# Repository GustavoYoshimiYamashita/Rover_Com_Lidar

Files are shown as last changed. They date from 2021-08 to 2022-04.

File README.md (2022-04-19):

# Rover_Com_Lidar
Um robô do tipo Rover com estrutura Rocker-bogie acoplado com um sensor Lidar
Avanço do Rover durante o ano de 2021

Etapas de desenvolvimento
1.	Estudo dos componentes eletrônicos necessários
2.	Modelagem 3D
3.	Desenvolvimento da montagem das peças
4.	Primeiros testes com o Lidar
5.	Primeiros testes com a estrutura Rocker-Bogie
6.	Modelagem de um sistema de encoders para as rodas
7.	Novo estudo sobre os microcontroladores e formas de comunicação
8.	Atualização e refinação da estrutura Rocker-Bogie
9.	Testes com a estrutura enfrentando desafios
10.	Correção de problemas com as rodas
11.	Correção do Motor de passo
12.	Estudo da geração de mapas para a visualização da nuvem de pontos do Lidar
13.	Novos testes com o Lidar funcionando
14.	Etapas completas, necessário o desenvolvimento de soluções para possíveis erros
15.	Problema “ainda” sem solução no giro da estrutura Rocker-Bogie
Componentes eletrônicos utilizados

## Modelagem 3D
Antes da aquisição dos materiais necessários para a montagem do Rover foi desenvolvido em um programa de modelagem 3D AutoCAD (SolidWorks) uma simulação da estrutura Rocker-Bogie, essa simulação permitiu uma visualização mais detalhada da aparência e dimensões finais do projeto antes mesmo da montagem. 

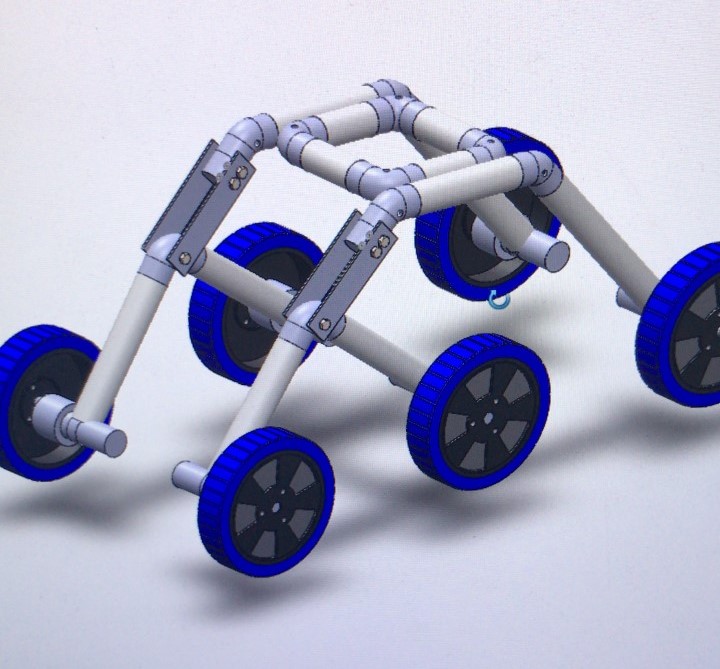
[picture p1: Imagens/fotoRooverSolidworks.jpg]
 
 
Dessa forma todo o processo pode ser visualizado de maneira que seja possível evitar erros na quantidade, formato ou tamanho dos materiais que serão utilizados, a importância dessa etapa está em precisar os custos do projeto e diminuir as chances de desperdício de tempo na correção de possíveis erros futuros decorrentes de uma visualização não apurada da montagem.

## Montagem e problemas iniciais 
Com base na modelagem 3D é possível iniciar a montagem seguindo o desenho como referência. Na primeira etapa então foi feito os cortes nos canos para o tamanho adequado, é importante destacar que se viu necessário manter uma das pontas reta com o mínimo de deformação, tendo em vista que essa parte se conectaria com o motor e qualquer desvio na estrutura deixaria o motor desalinhado e com o seu giro prejudicado quando comparado com os outros motores.
Sem um kit profissional de corte e lixamento o processo se torna demorado e cansativo, porém é possível ser realizado utilizando-se de ferramentas como serras e lixas de papel.

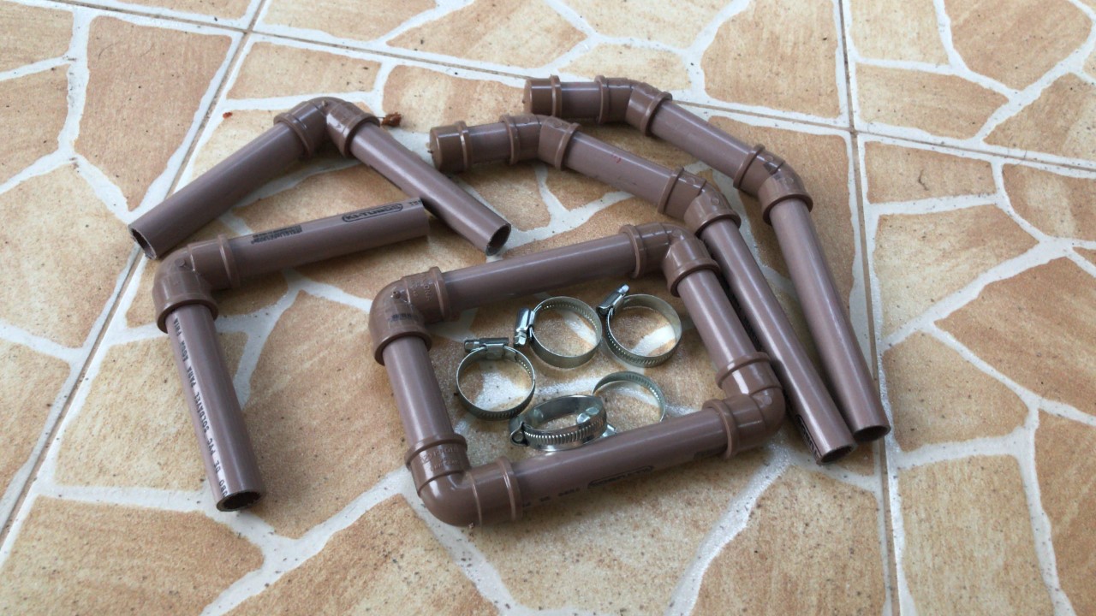
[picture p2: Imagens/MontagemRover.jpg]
Foto da montagem


Com os cortes feitos, bastava apenas a montagem.

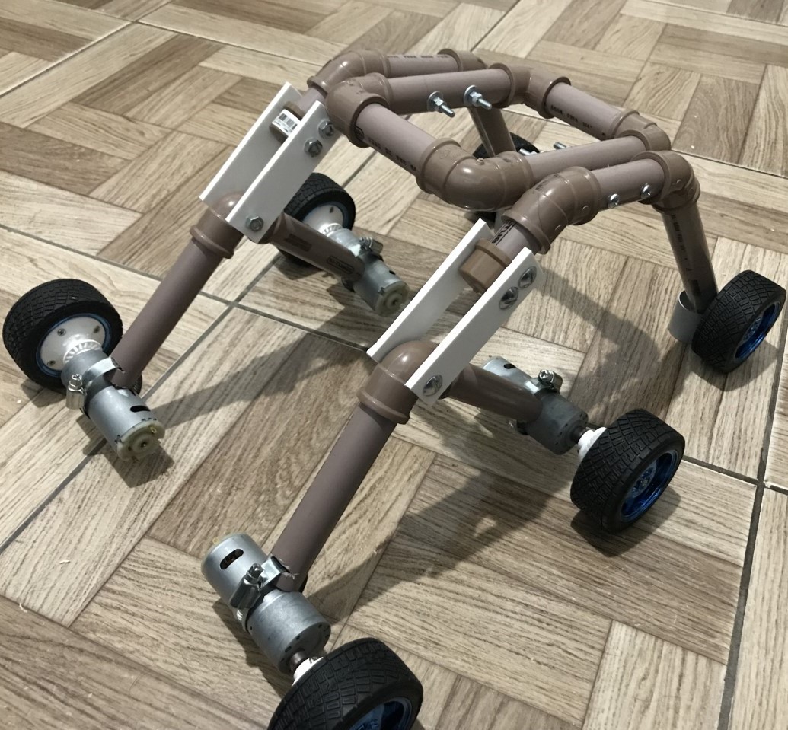
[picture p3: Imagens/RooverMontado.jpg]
Foto do rover montado

 
A montagem ficou idêntica a simulação feita no SolidWorks, porém, nos primeiros testes realizados ficou evidente alguns problemas da estrutura. Os furos no qual passavam os parafusos que conectavam as partes de cima estavam desalinhados e por isso ocasionaram um erro que impedia a realização de movimentos mais complexos como por exemplo subir uma escada. 
As rodas evidenciaram outro problema ocasionado pelo método escolhido para prender a roda com o motor, o eixo do motor estava deslizando sem prender na roda, dessa forma, quando o motor se encontrava em uma região de alto atrito ou que necessitava de um alto torque as rodas giravam e falso.
No lidar a estrutura se comportou de maneira no qual havia sido prevista, não demonstrando então problemas ou erros aparentes.

Foto do Lidar montado
 
Um desafio enfrentado no projeto foi nos testes realizados no motor de passo Nema 17, que ao comprar pela internet possuía em suas características um certo nível de torque mais que necessário para a estrutura em si, porém, quando o pacote chegou o motor se demonstrou diferente das características anunciadas. Devido a esse motivo a etapa de desenvolvimento do Lidar foi prejudica, já que foram testados diversos códigos diferentes com o pensamento de que o problema não era no hardware (por causa da falsa informação do anúncio), por fim foi decidido a compra de um novo motor de passo do tipo Nema 17 que não apresentou problema nenhum e funcionou perfeitamente.
Desenvolvimento da estrutura Rocker-Bogie

O falso giro das rodas impedia que o robô conseguisse executar tarefas mais difíceis como subir escadas, superar obstáculos e se movimentar em terrenos irregulares. A solução encontrada para este problema foi modelar um encaixe que se prendesse ao eixo do motor sem a necessidade de um parafuso ou material adesivo, para isso foi desenhado a entrada do suporte com o mesmo formato e dimensão do eixo do motor.
Para corrigir o desalinhamento da estrutura Rocker-Bogie foi necessário reconstruir todo o robô com novos materiais, além disso foi utilizado um cano mais grosso já que no primeiro caso a ruptura de alguns pontos eram comuns devido a espessura dos canos antes utilizados, dessa forma, a substituição dos materiais serviu não apenas para corrigir o alinhamento, mas também para garantir maior resistência do robô.

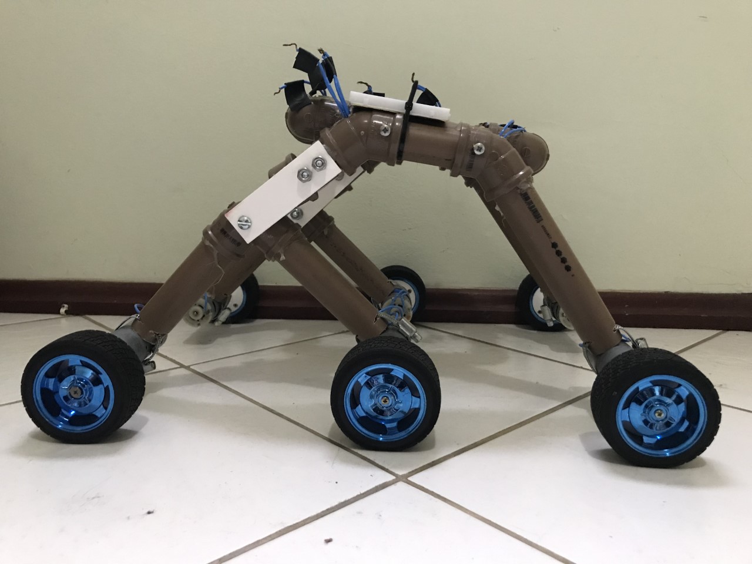
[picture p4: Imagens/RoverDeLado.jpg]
Foto da versão 2 do Rover

 
Nesse novo modelo a estrutura se apresentou eficiente no desenvolvimento de obstáculos e caminhos mais complexos, com os 6 motores somando um total de 60kg de torque, não houve nenhum problema de movimentação decorrente do peso total do robô. 

## Desenvolvimento do Lidar

O objetivo do Lidar era criar uma nuvem de pontos provenientes das leituras do sensor Infravermelho utilizado, o TF-Luna. Esse sensor possui um alcance significativamente alto quando comparado com outros modelos encontrados para comprar, com uma leitura de 8 metros esse sensor é capaz de mapear ambientes grandes sem a necessidade de se deslocar.
No começo do projeto foi pensado em utilizar algum sistema para enviar as leituras do sensor via bluetooth ou Wifi, com o objetivo de proporcionar maior articulação sem a necessidade do uso de algum fio de conexão, no entanto, foi optado o uso de uma conexão USB com o computador pois alguns problemas de envio de dados estavam sendo enfrentados na opção de Wifi ou Bluetooth. Dessa forma, o Lidar está funcionando conectado por um cabo USB ao computador, porém, isso foi previsto e pensado como uma situação coerente com o desenvolvimento do projeto esse ano, com o objetivo de nos próximos passos modificar a estrutura lógica para então utilizar um sistema sem fio. Pela imagem abaixo podemos ver o Lidar conectado ao computador.

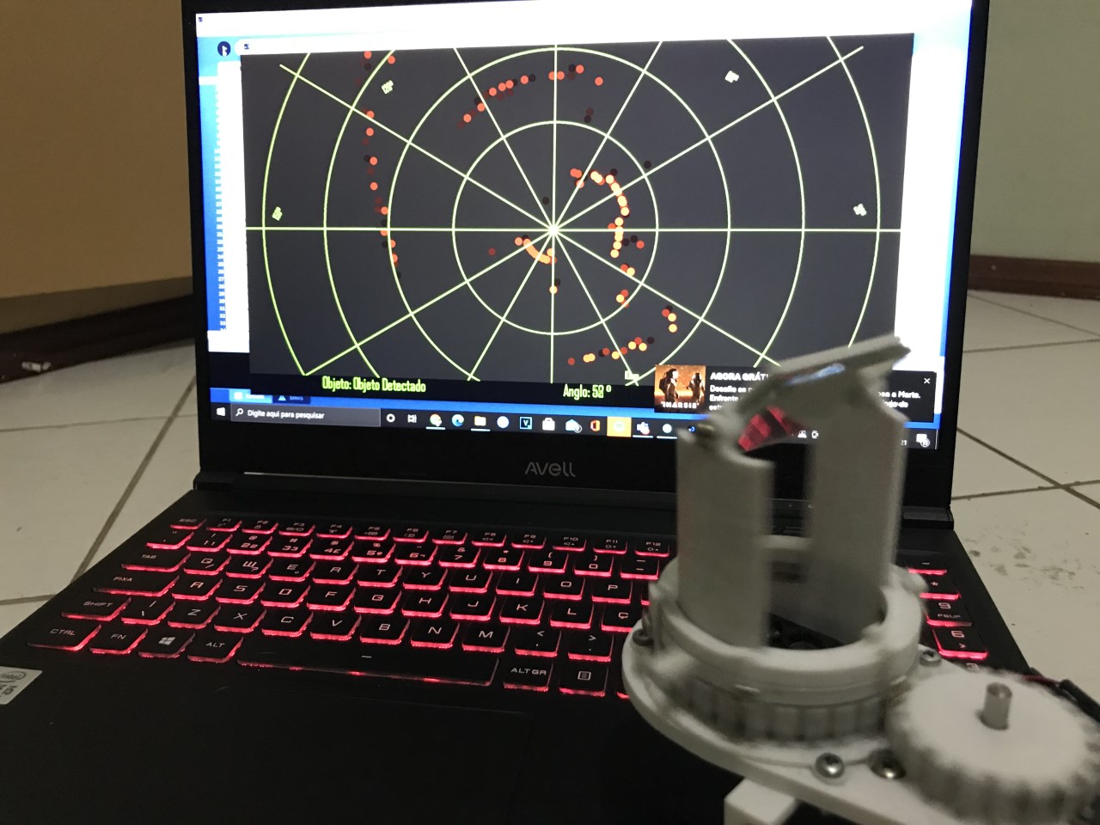
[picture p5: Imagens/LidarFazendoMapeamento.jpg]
Picture of the 3D lidar


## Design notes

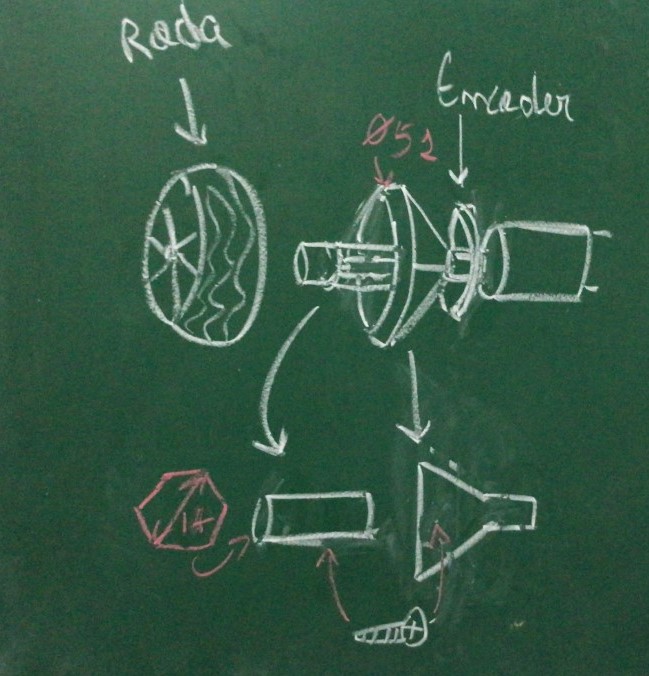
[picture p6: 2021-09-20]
Imagens/LousaDesenhos.jpg

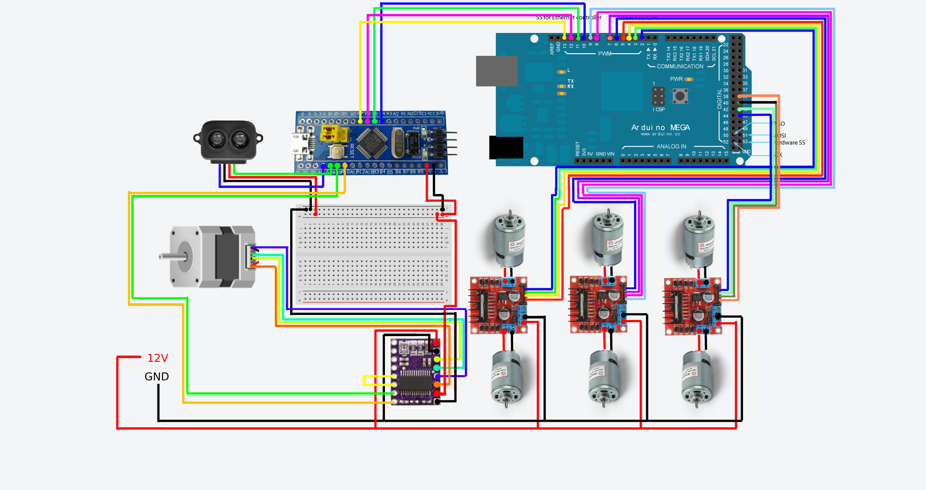
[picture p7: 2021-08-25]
Circuito/Circuito Principal/conexõesRover.png

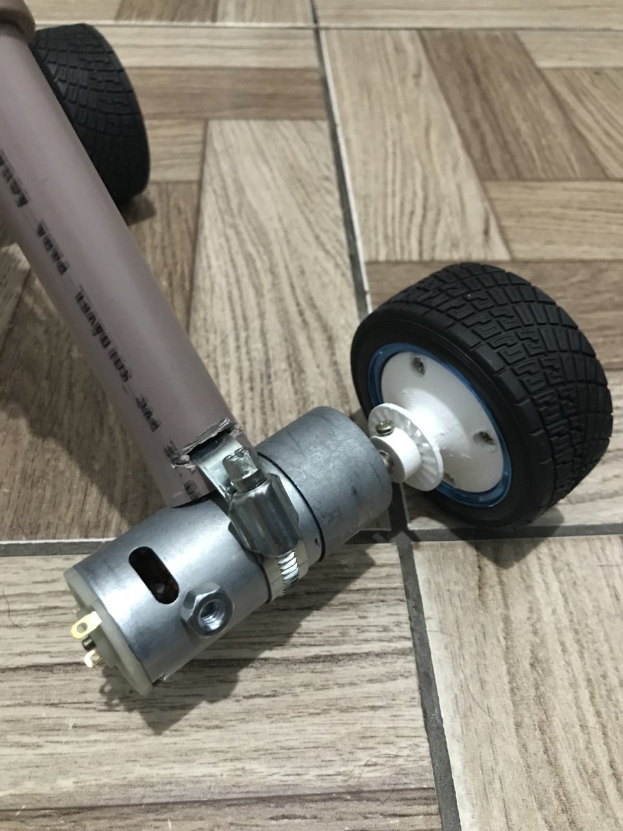
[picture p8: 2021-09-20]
Imagens/encaixeCompletoRodas.jpg

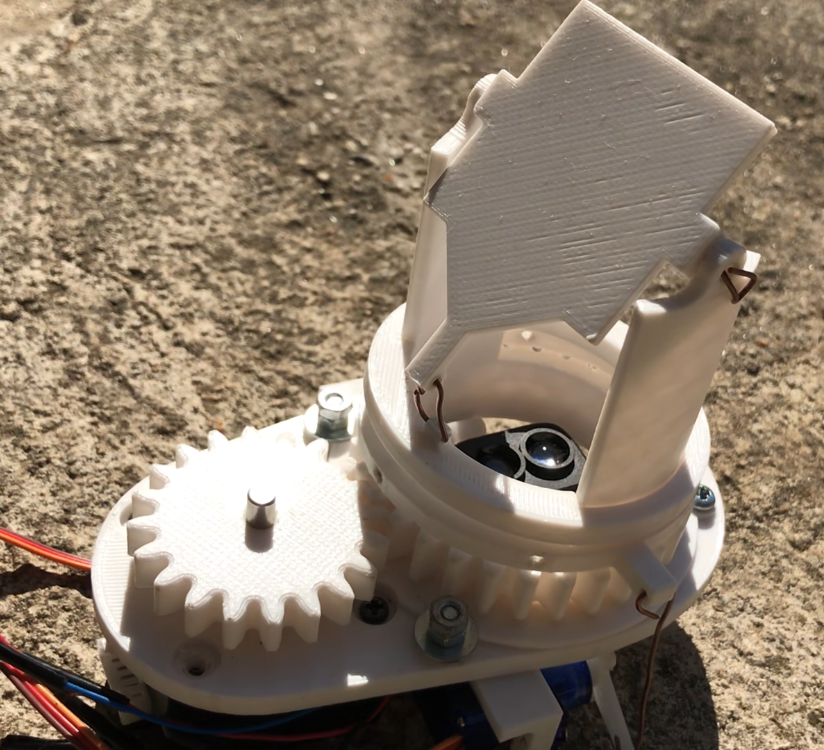
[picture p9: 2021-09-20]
Imagens/Foto1Lidar.png

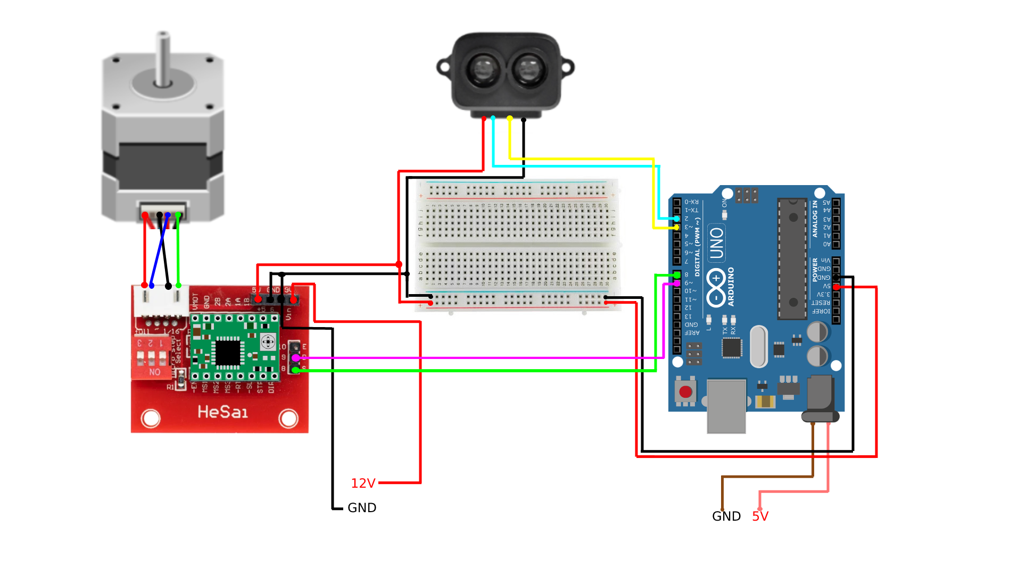
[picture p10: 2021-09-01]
Circuito/Circuito Lidar-Motor De Passo-Arduino/Novo Projeto.png

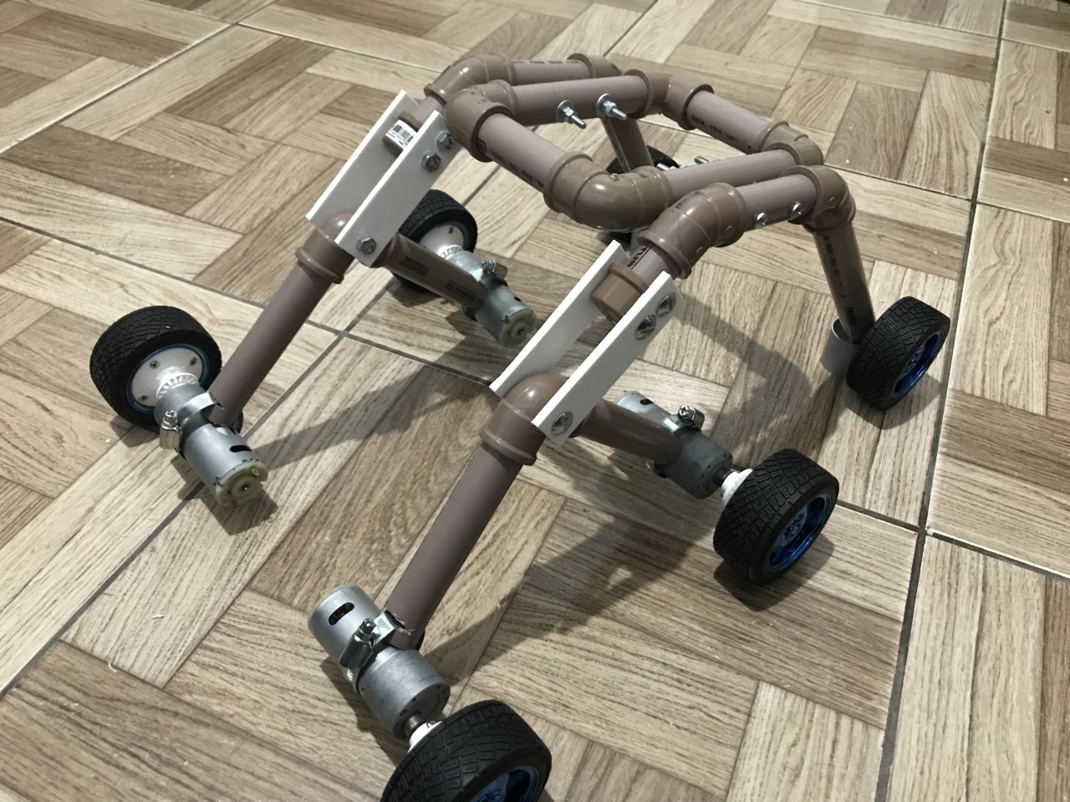
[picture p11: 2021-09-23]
Imagens/roverComProblema.jpg

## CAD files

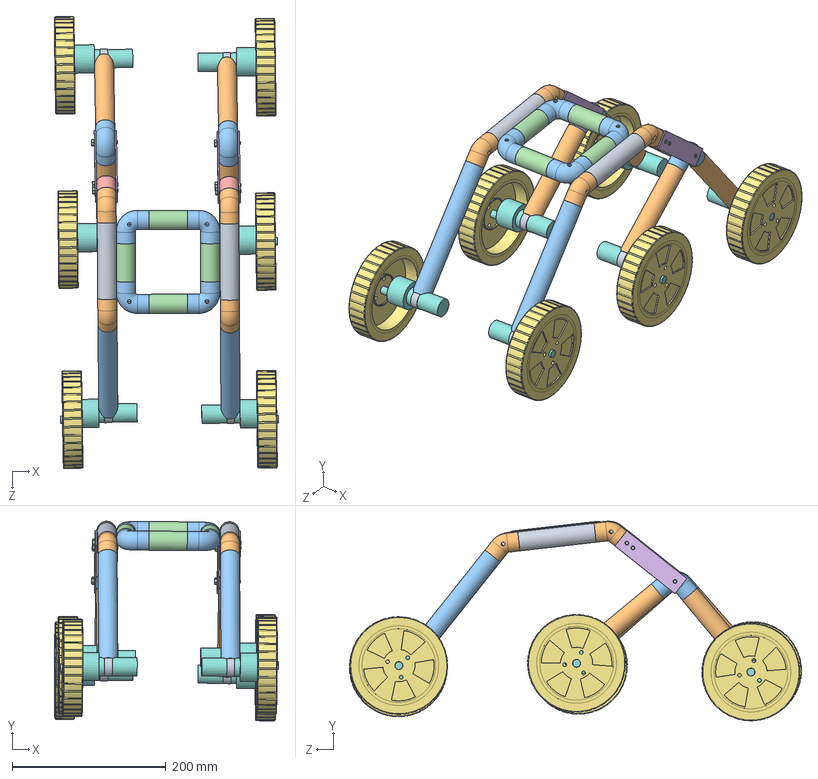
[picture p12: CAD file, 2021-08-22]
Partes 3D/Rover/Montagem1.SLDASM
292.2 x 260.0 x 588.8 mm
Cano10cm x 2
Cotovelo45graus x 4
Cotovelo90graus x 6
hex cap screw_am x 6
CapaPVC x 2
placaDeApoio x 4
Cytron 5 Inches Robot Wheel x 6
Motor12VDC x 6
EnforcaGato x 6
Cano13cm x 4
Cano18cm x 2
Cano5cm x 4

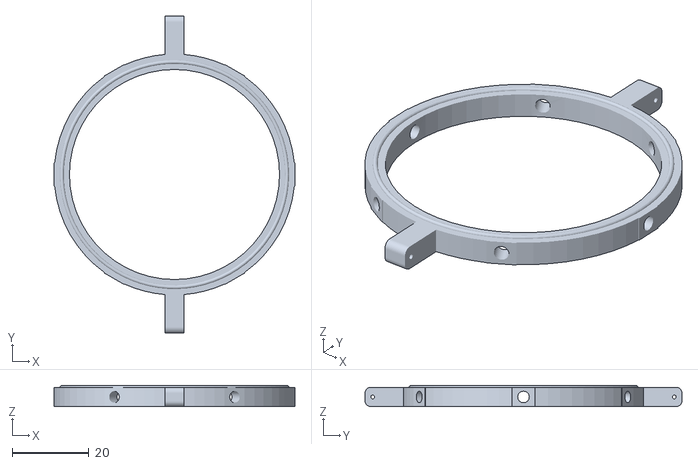
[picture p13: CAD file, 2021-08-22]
Partes 3D/Lidar/LidarMK2-Ring_bot.STL
62.6 x 82.4 x 5.50

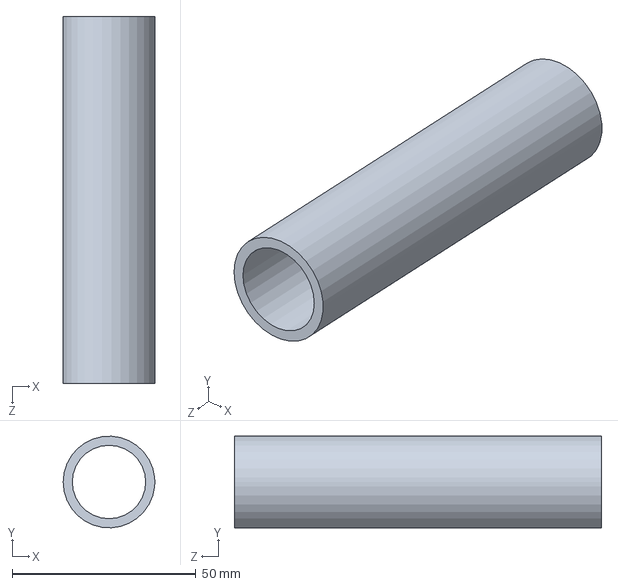
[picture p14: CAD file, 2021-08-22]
Partes 3D/Rover/Cano10cm.SLDPRT
25.0 x 25.0 x 100.0 mm

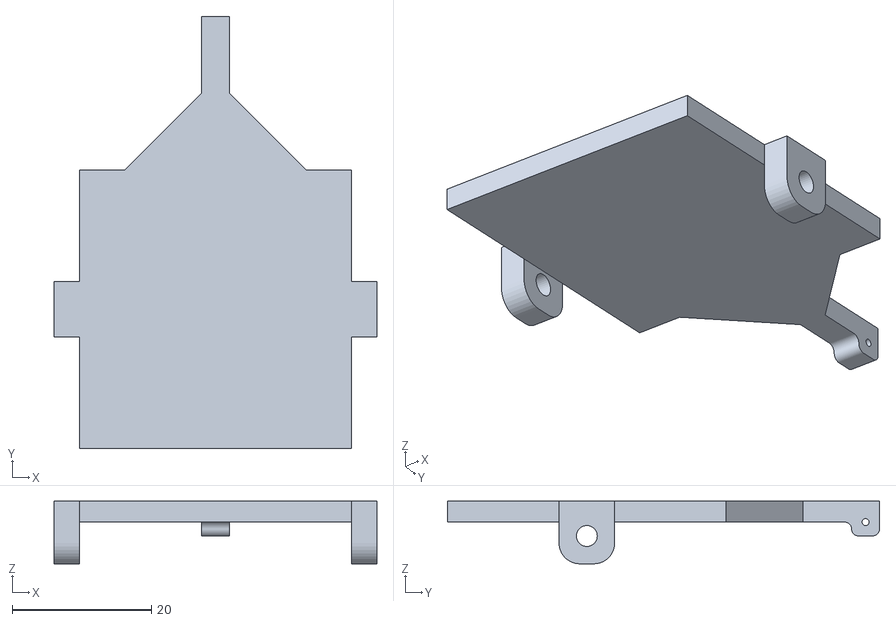
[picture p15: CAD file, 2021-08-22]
Partes 3D/Lidar/LidarMK2-Mirror.STL
46.3 x 62.0 x 9.00

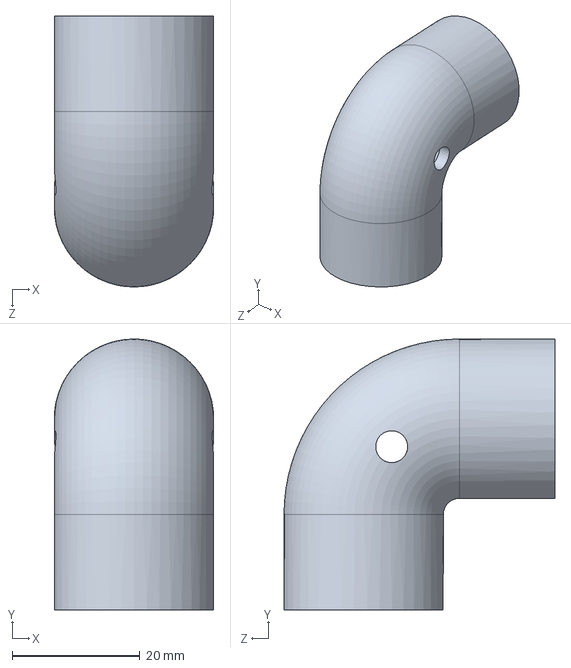
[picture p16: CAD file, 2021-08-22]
Partes 3D/Rover/Cotovelo90graus.SLDPRT
25.0 x 42.5 x 42.5 mm

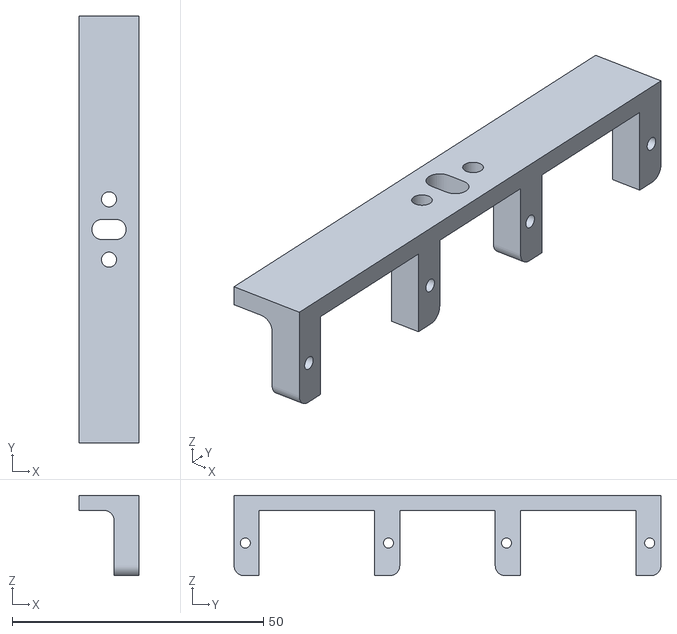
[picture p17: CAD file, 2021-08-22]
Partes 3D/Lidar/LidarMK2-Servos.STL
12.0 x 85.0 x 16.0

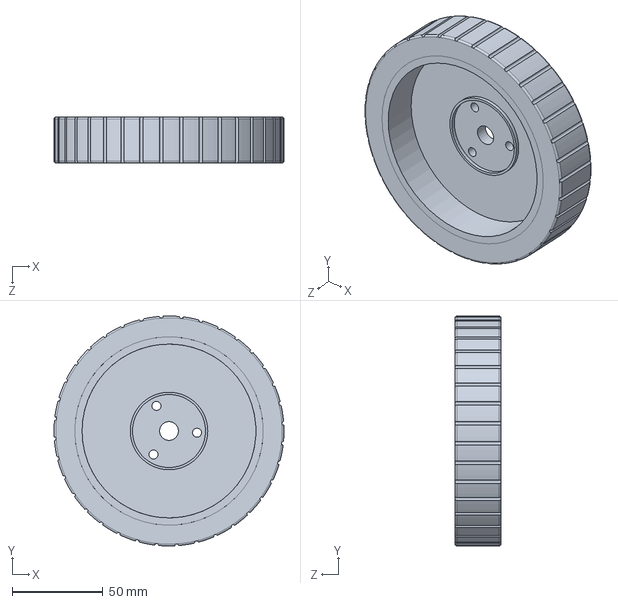
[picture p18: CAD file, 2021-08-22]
Partes 3D/Rover/Cytron 5 Inches Robot Wheel.SLDPRT
127.0 x 127.0 x 25.4 mm

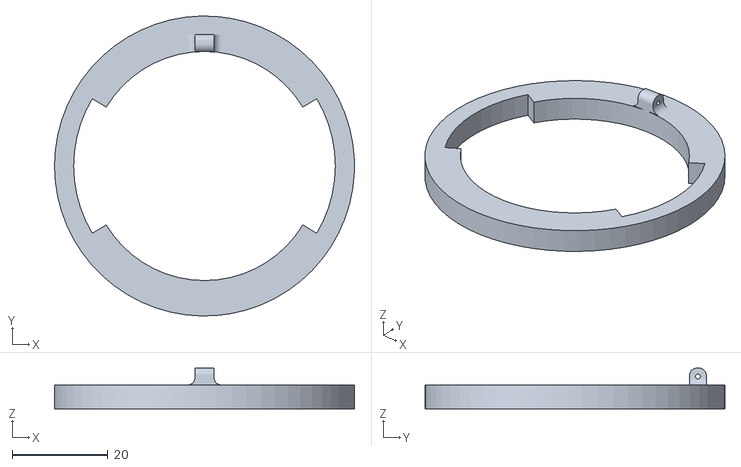
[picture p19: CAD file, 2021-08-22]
Partes 3D/Lidar/LidarMK2-Ring_top.STL
62.6 x 62.6 x 8.50

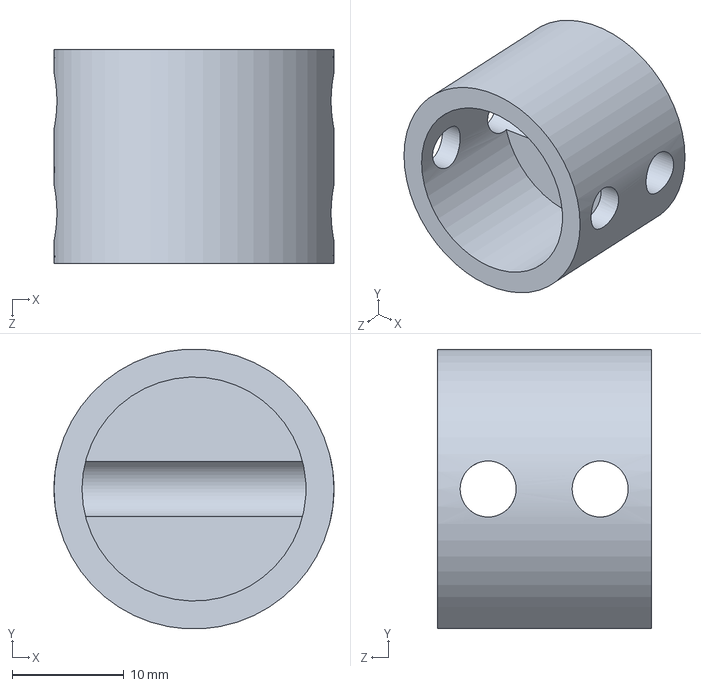
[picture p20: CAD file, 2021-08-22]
Partes 3D/Rover/CapaPVC.SLDPRT
25.0 x 25.0 x 19.1 mm

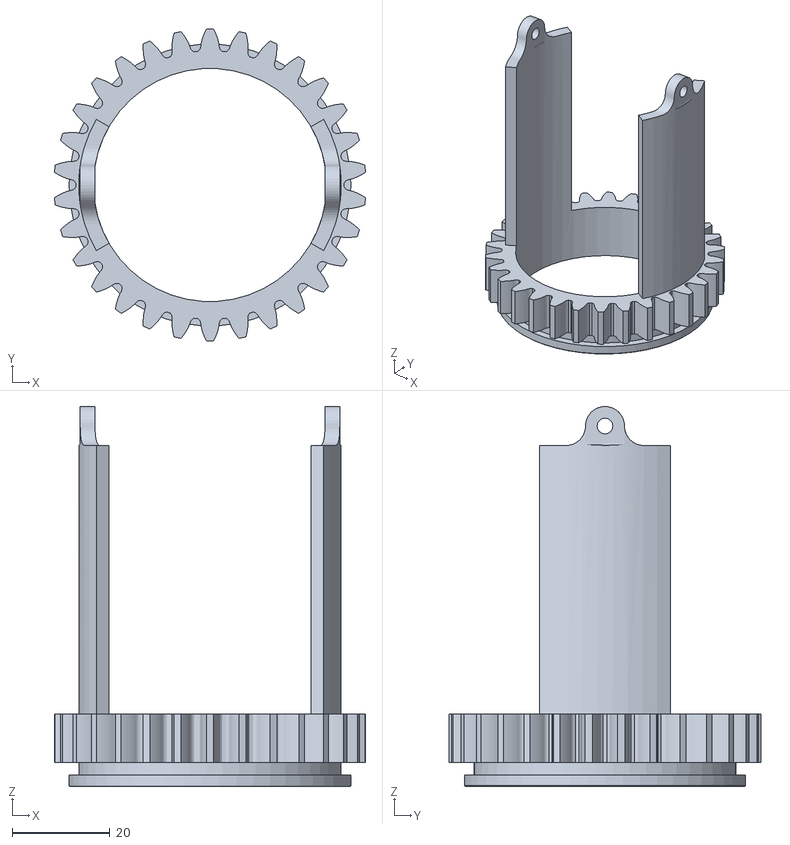
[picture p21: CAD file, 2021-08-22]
Partes 3D/Lidar/LidarMK2-Rotor.STL
63.8 x 64.0 x 77.9

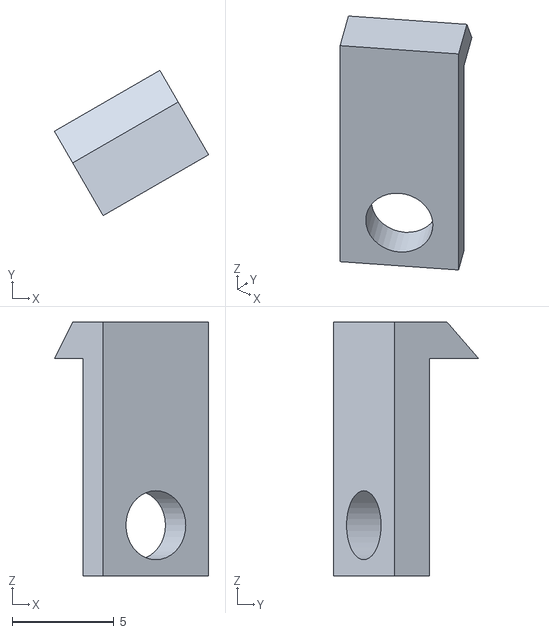
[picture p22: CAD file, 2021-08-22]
Partes 3D/Lidar/LidarMK2-Ring_link.STL
7.60 x 7.16 x 12.5

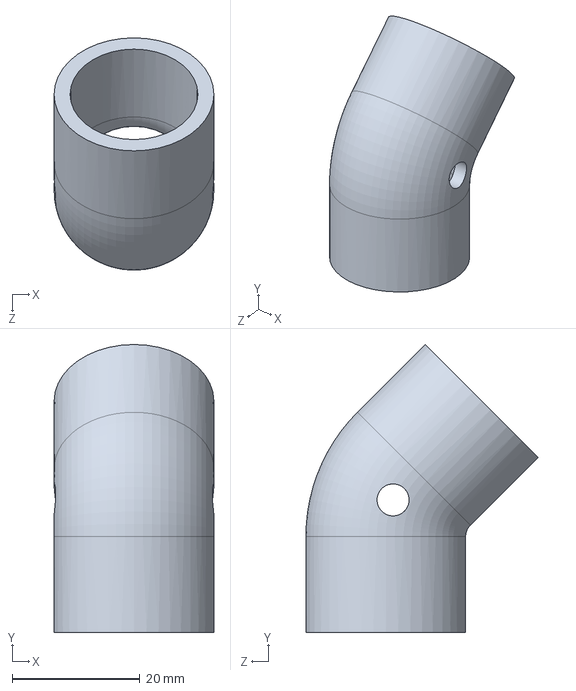
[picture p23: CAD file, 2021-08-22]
Partes 3D/Rover/Cotovelo45graus.SLDPRT
25.0 x 45.1 x 36.3 mm

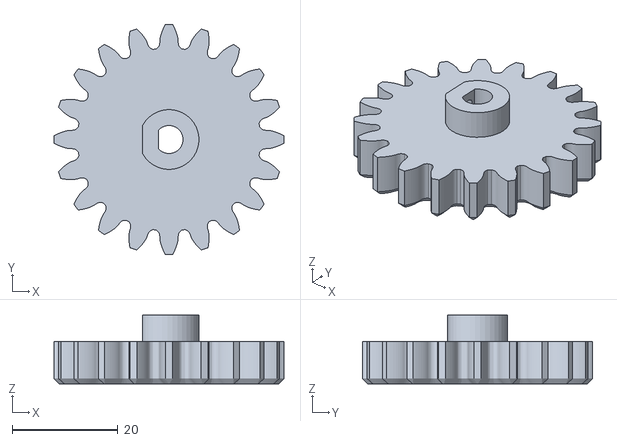
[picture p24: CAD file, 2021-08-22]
Partes 3D/Lidar/LidarMK2-GearMotor.STL
43.4 x 43.4 x 13.0

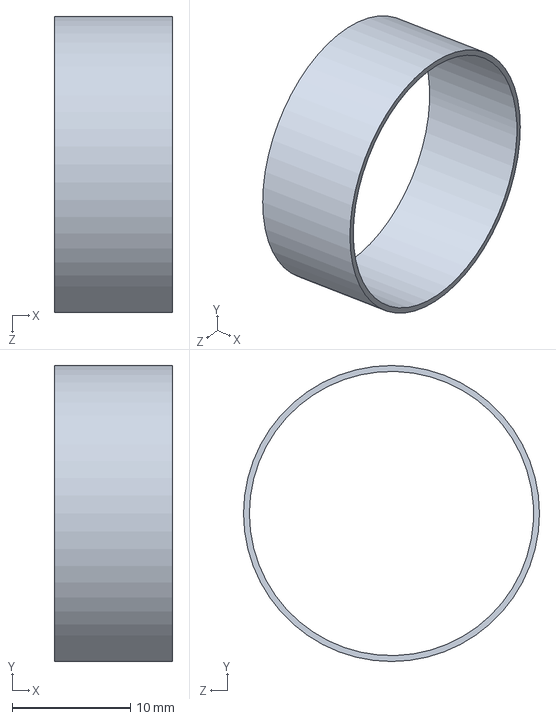
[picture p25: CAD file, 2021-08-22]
Partes 3D/Rover/EnforcaGato.SLDPRT
10.0 x 25.0 x 25.0 mm

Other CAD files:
Partes 3D/Lidar/LidarMK2-Base.STL
Partes 3D/Rover/Cano5cm.SLDPRT
Partes 3D/Lidar/LidarMK2.SLDPRT
Partes 3D/Rover/Cano9cm.SLDPRT
Partes 3D/Lidar/LidarMK2-Rotor _holder.STL
Partes 3D/Rover/Cano13cm.SLDPRT
Partes 3D/Rover/Cano15cm.SLDPRT
Partes 3D/Rover/Cano18cm.SLDPRT
Partes 3D/Rover/Motor12VDC.SLDPRT
Partes 3D/Rover/placaDeApoio.SLDPRT

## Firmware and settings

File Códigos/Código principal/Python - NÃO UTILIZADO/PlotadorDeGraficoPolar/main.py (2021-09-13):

# Python + Arduino-based Radar Plotter
#
# ** Works with any motor that outputs angular rotation
# ** and with any distance sensor (HC-SR04, VL53L0x,LIDAR)
#
import numpy as np
import matplotlib

matplotlib.use('TkAgg')
import matplotlib.pyplot as plt
from matplotlib.widgets import Button
import serial, sys, glob
import serial.tools.list_ports as COMs


#
#
############################################
# Find Arudino ports, select one, then start communication with it
############################################
#
def port_search():
    if sys.platform.startswith('win'):  # Windows
        ports = ['COM{0:1.0f}'.format(ii) for ii in range(1, 256)]
    elif sys.platform.startswith('linux') or sys.platform.startswith('cygwin'):
        ports = glob.glob('/dev/tty[A-Za-z]*')
    elif sys.platform.startswith('darwin'):  # MAC
        ports = glob.glob('/dev/tty.*')
    else:
        raise EnvironmentError('Machine Not pyserial Compatible')

    arduinos = []
    for port in ports:  # loop through to determine if accessible
        if len(port.split('Bluetooth')) > 1:
            continue
        try:
            ser = serial.Serial(port)
            ser.close()
            arduinos.append(port)  # if we can open it, consider it an arduino
        except (OSError, serial.SerialException):
            pass
    return arduinos


arduino_ports = port_search()
ser = serial.Serial(arduino_ports[1], baudrate=115200)  # match baud on Arduino
ser.flush()  # clear the port
#
############################################
# Start the interactive plotting tool and
# plot 180 degrees with dummy data to start
############################################
#
fig = plt.figure(facecolor='k')
win = fig.canvas.manager.window  # figure window
screen_res = win.wm_maxsize()  # used for window formatting later
dpi = 150.0  # figure resolution
fig.set_dpi(dpi)  # set figure resolution

# polar plot attributes and initial conditions
ax = fig.add_subplot(111, polar=True, facecolor='#006d70')
ax.set_position([-0.05, -0.05, 1.1, 1.05])
r_max = 100.0  # can change this based on range of sensor
ax.set_ylim([0.0, r_max])  # range of distances to show
ax.set_xlim([0.0, np.pi])  # limited by the servo span (0-180 deg)
ax.tick_params(axis='both', colors='w')
ax.grid(color='w', alpha=0.5)  # grid color
ax.set_rticks(np.linspace(0.0, r_max, 5))  # show 5 different distances
ax.set_thetagrids(np.linspace(0.0, 180.0, 10))  # show 10 angles
angles = np.arange(0, 181, 1)  # 0 - 180 degrees
theta = angles * (np.pi / 180.0)  # to radians
dists = np.ones((len(angles),))  # dummy distances until real data comes in
pols, = ax.plot([], linestyle='', marker='o', markerfacecolor='w',
                markeredgecolor='#EFEFEF', markeredgewidth=1.0,
                markersize=10.0, alpha=0.9)  # dots for radar points
line1, = ax.plot([], color='w',
                 linewidth=4.0)  # sweeping arm plot

# figure presentation adjustments
fig.set_size_inches(0.96 * (screen_res[0] / dpi), 0.96 * (screen_res[1] / dpi))
plot_res = fig.get_window_extent().bounds  # window extent for centering
win.wm_geometry('+{0:1.0f}+{1:1.0f}'. \
                format((screen_res[0] / 2.0) - (plot_res[2] / 2.0),
                       (screen_res[1] / 2.0) - (plot_res[3] / 2.0)))  # centering plot
fig.canvas.toolbar.pack_forget()  # remove toolbar for clean presentation
fig.canvas.set_window_title('Arduino Radar')

fig.canvas.draw()  # draw before loop
axbackground = fig.canvas.copy_from_bbox(ax.bbox)  # background to keep during loop


############################################
# button event to stop program
############################################

def stop_event(event):
    global stop_bool
    stop_bool = 1


prog_stop_ax = fig.add_axes([0.85, 0.025, 0.125, 0.05])
pstop = Button(prog_stop_ax, 'Stop Program', color='#FCFCFC', hovercolor='w')
pstop.on_clicked(stop_event)


# button to close window
def close_event(event):
    global stop_bool, close_bool
    if stop_bool:
        plt.close('all')
    stop_bool = 1
    close_bool = 1


close_ax = fig.add_axes([0.025, 0.025, 0.125, 0.05])
close_but = Button(close_ax, 'Close Plot', color='#FCFCFC', hovercolor='w')
close_but.on_clicked(close_event)

fig.show()

############################################
# inifinite loop, constantly updating the
# 180deg radar with incoming Arduino data
############################################
#
start_word, stop_bool, close_bool = False, False, False
while True:
    try:
        if stop_bool:  # stops program
            fig.canvas.toolbar.pack_configure()  # show toolbar
            if close_bool:  # closes radar window
                plt.close('all')
            break
        ser_bytes = ser.readline()  # read Arduino serial data
        decoded_bytes = ser_bytes.decode('utf-8')  # decode data to utf-8
        data = (decoded_bytes.replace('\r', '')).replace('\n', '')
        if start_word:
            vals = [float(ii) for ii in data.split(',')]
            if len(vals) < 2:
                continue
            angle, dist = vals  # separate into angle and distance
            if dist > r_max:
                dist = 0.0  # measuring more than r_max, it's likely inaccurate
            dists[int(angle)] = dist
            if angle % 5 == 0:  # update every 5 degrees
                pols.set_data(theta, dists)
                fig.canvas.restore_region(axbackground)
                ax.draw_artist(pols)

                line1.set_data(np.repeat((angle * (np.pi / 180.0)), 2),
                               np.linspace(0.0, r_max, 2))
                ax.draw_artist(line1)

                fig.canvas.blit(ax.bbox)  # replot only data
                fig.canvas.flush_events()  # flush for next plot
        else:
            if data == 'Radar Start':  # stard word on Arduno
                start_word = True  # wait for Arduino to output start word
                print('Radar Starting...')
            else:
                continue

    except KeyboardInterrupt:
        plt.close('all')
        print('Keyboard Interrupt')
        break

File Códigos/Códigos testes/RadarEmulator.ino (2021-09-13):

#include <Servo.h>

Servo servo_1; // servo controller (multiple can exist)

int trig = 4; // trig pin for HC-SR04
int echo = 5; // echo pin for HC-SR04
int servo_pin = 3; // PWM pin for servo control

int pos = 0;    // servo starting position
float duration,distance;

void setup() {
  Serial.begin(115200);
  Serial.println("Radar Start");
  servo_1.attach(servo_pin); // start servo control
  pinMode(trig,OUTPUT);
  pinMode(echo,INPUT);
}

void loop() {
  for (pos = 0; pos <= 180; pos += 1) { // goes from 0 degrees to 180 degrees
    // in steps of 1 degree
    servo_1.write(pos);              // tell servo to go to position in variable 'pos'
    delay(60); // delay to allow the servo to reach the desired position
    dist_calc(pos);
  }
 
  for (pos = 180; pos >= 0; pos -= 1) { // goes from 180 degrees to 0 degrees
    servo_1.write(pos);              // tell servo to go to position in variable 'pos'
    delay(60);
    dist_calc(pos);
  }
}

float dist_calc(int pos){
  // trigger 40kHz pulse for ranging
  digitalWrite(trig,LOW);
  delayMicroseconds(2);
  digitalWrite(trig,HIGH);
  delayMicroseconds(10);
  digitalWrite(trig,LOW);
  // convert from duration for pulse to reach detector (microseconds) to range (in cm)
  duration = pulseIn(echo,HIGH); // duration for pulse to reach detector (in microseconds)
  distance = 100.0*(343.0*(duration/2.0))/1000000.0; // 100.0*(speed of sound*duration/2)/microsec conversion
 
  Serial.print(pos); // position of servo motor
  Serial.print(","); // comma separate variables
  Serial.println(distance); // print distance in cm
}

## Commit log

2021-08-22 Commite inicial
    [Cano10cm.SLDPRT, Cano13cm.SLDPRT, Cano15cm.SLDPRT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]
2021-08-22 Incluindo imagem do circuito
2021-08-22 Mudando a foto do circuito
2021-09-01 adicionando circuito novo
2021-09-15 atualizaçao nos códigos, mudança de python para processing com o objetivo de plotar um gráfico polar estilo radar
2021-09-20 atualizando o código do gerador de mapa, agora para o modelo cartesiano, inserindo novas imagens e vídeos
2022-04-19 Update README.md
    Adicionando texto do lidar
